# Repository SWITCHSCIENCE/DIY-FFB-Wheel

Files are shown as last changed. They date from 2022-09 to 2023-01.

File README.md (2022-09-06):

# DIY-FFB-Wheel

自作フォースフィードバックステアリングホイール

## 必要なもの

- 「[Arduino Leonard(入出力 5V)](https://www.switch-science.com/catalog/968/)」または「[Pro micro(入出力 5V)](https://www.switch-science.com/catalog/3914/)」などの「Atmega32UX」系列の Arduino 対応ボード
- [Waveshare の CAN for RaspberryPi Pico ボード(入出力 3.3V)](https://www.waveshare.com/pico-can-a.htm)
- [レベル変換ボード(3.3V 系と 5V 系をつなぐ)](https://www.switch-science.com/catalog/1523/)
- [DDT インホイールモーター](https://www.switch-science.com/catalog/8248/)
- [24V20A 安定化電源ユニット](https://www.amazon.co.jp/gp/product/B09PRD74V4)

## ファームウェアビルド

### 必要なライブラリ

- QuickPID(MIT-Licence)
- ArduinoJoystickWithFFB(LGPL-ICENCE)

上記２つのライブラリをライブラリマネージャから探してあらかじめインストールしておいてください。
ArduinoJoystickWithFFB は検索でも見つからないので、以下の操作でインストールしてください。

```コマンドプロンプト
winget install Git # <-まだgitコマンドが使えない場合のみ実行してください
cd C:\Users\<ユーザー名>\Documents\Arduino\libraries
git clone https://github.com/YukMingLaw/ArduinoJoystickWithFFBLibrary
```

## ボードサポートのインストール

Arduino-IDE または Arduino-IDE-V2 または arduino-cli のいずれも利用可能です。
core サポートのインストールが必要です。「Arduino AVR Boards Support」を検索してインストールが必要です。

arduino-cli の場合は以下の操作でコアサポートインストールを行います。

コアサポートインストール

```コマンドプロンプト
arduino-cli core install arduuino:avr
```

## ビルドとフラッシュ

arduino-cli の場合

PC と Arduino-Leonard を USB マイクロケーブルで接続しておいて以下のコマンドでビルドと書き込み。

```コマンドプロンプト
cd firmware
make build flash
```

## 配線

| 名称 | Arduino Leonard | レベル変換 H 側 | レベル変換 L 側 | CAN アダプタ |
| --- | --- | --- | --- | --- |
| RX | 0 番 | HV1 | LV1 | GP1/RX |
| TX | 1 番 | HV2 | LV2 | GP0/TX |
| Config | 2 番 | HV3 | LV3 | GP2 |
| Reset  | 3 番 | HV4 | LV4 | GP3 |
| 5V | 5V | HV | - | VSYS |
| 3.3V | 3.3V | - | LV | - |
| GND | GND | GND | GND | GND |

| 名称 | 電源ユニット | モーター | CAN アダプタ |
| --- | --- | --- | --- |
| プラス | プラス | 赤 | - |
| マイナス | マイナス | 黒 | - |
| CAN-H | - | 黄色 | H |
| CAN-L | - | 白色 | L |
| コンセント H | AC-H | - | - |
| コンセント C | AC-C | - | - |
| コンセント E | AC-E | - | - |

## 3D モデル

- ステアリングバックプレート: steering.stl
- 固定台： holder.stl

双方を[JLCPCB](https://www.pcbway.jp/)にてプリントしてもらう場合は以下のような見積もりになりました。

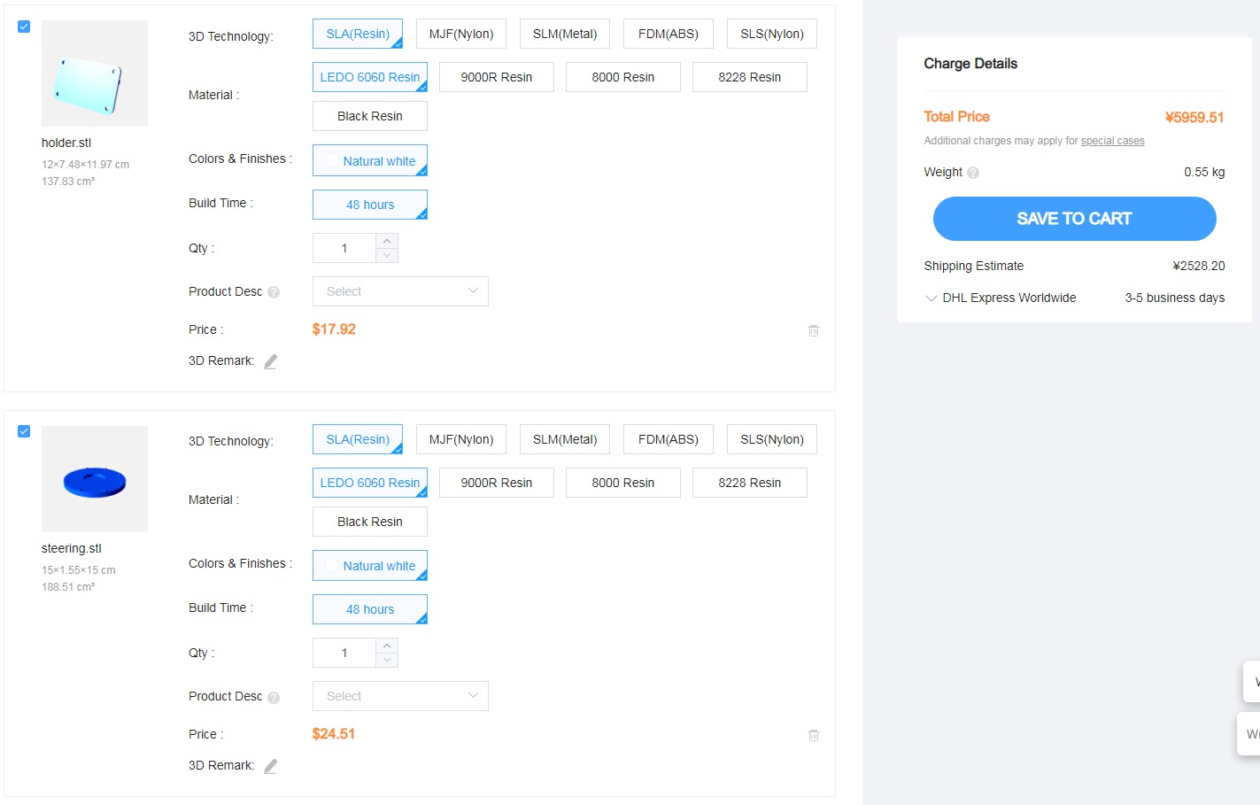
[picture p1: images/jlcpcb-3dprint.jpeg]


SLA 方式にてオーダーした場合、8600 円弱（送料込み） という試算でした。

### その他必要な部品

- M5x20mm ボルト＆ナットセット６本
- M6x20mm ボルト６本

モーターとステアリングバックプレートの固定にはタイヤを外した時のねじをそのまま使います。

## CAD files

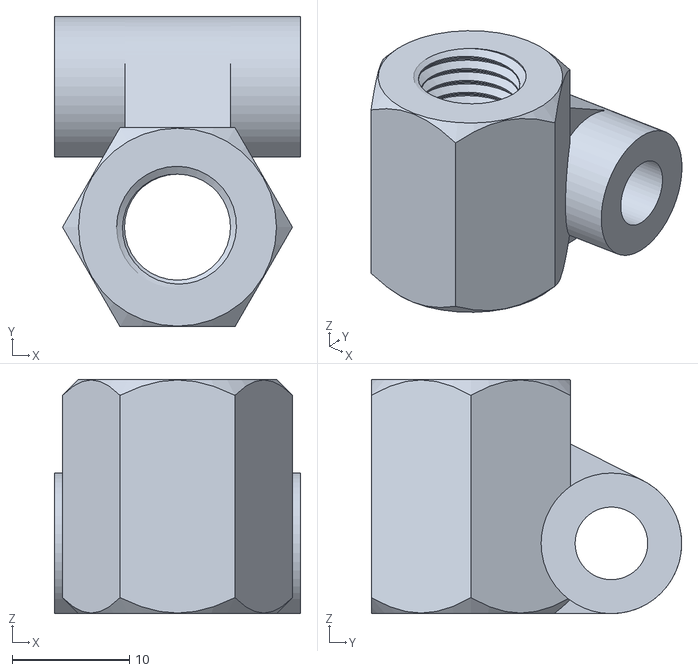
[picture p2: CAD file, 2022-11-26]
models/pedals/for-air-cylinder/air-rod-holder.stl
21.0 x 26.5 x 20.0

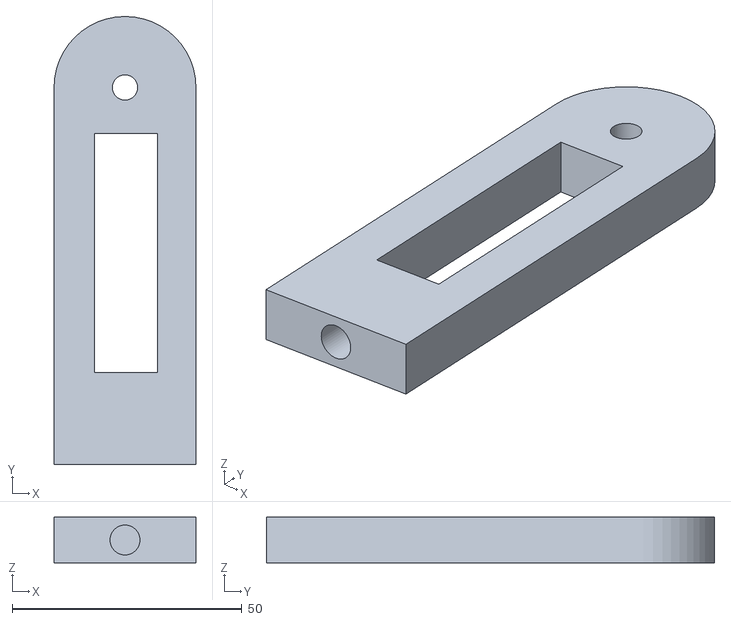
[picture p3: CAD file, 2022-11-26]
models/pedals/for-clutch/rod-angle2.stl
30.9 x 97.4 x 10.0

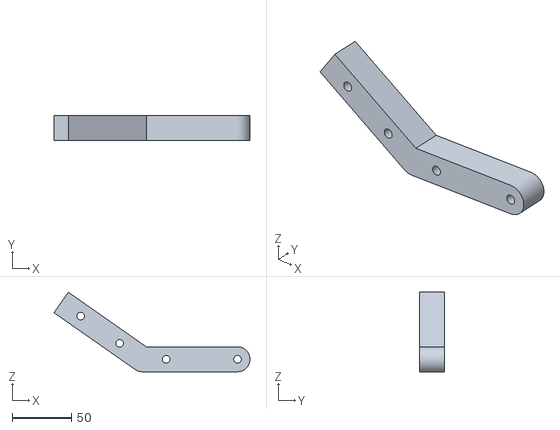
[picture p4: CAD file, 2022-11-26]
models/pedals/for-handbrake/sb-grip-rod.stl
164.8 x 21.0 x 66.9

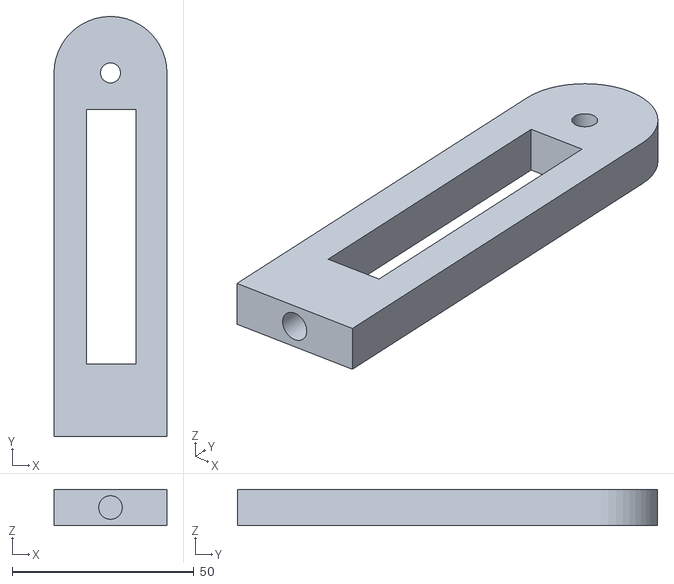
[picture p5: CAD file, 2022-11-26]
models/pedals/for-throttle/rod-angle.stl
31.1 x 115.5 x 10.0

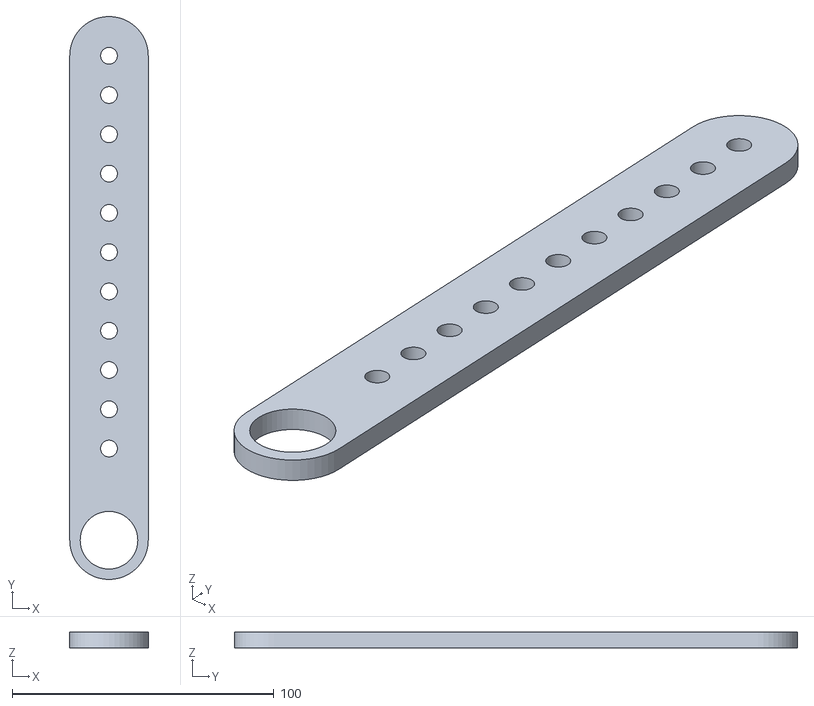
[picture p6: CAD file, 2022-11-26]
models/pedals/pedal-arm.stl
30.0 x 215.0 x 6.00

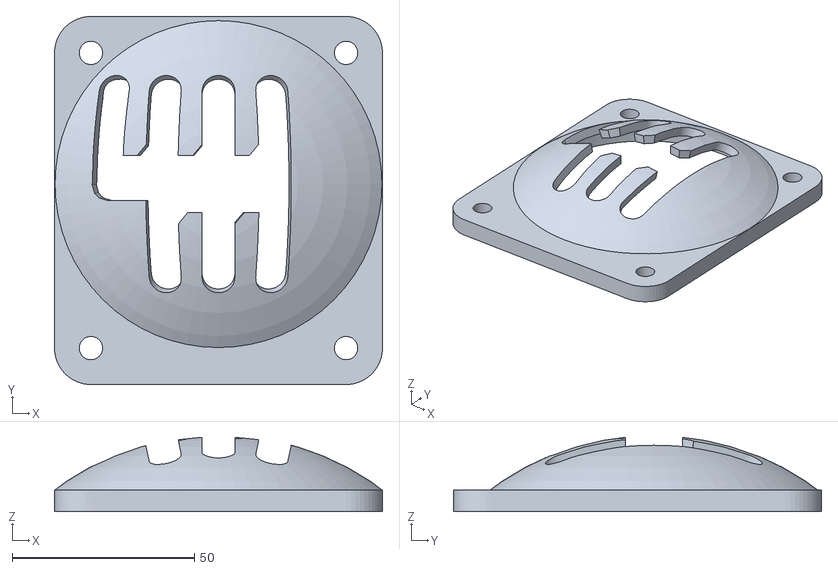
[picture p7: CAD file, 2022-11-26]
models/shifter/h-shifter-top.stl
90.0 x 101.0 x 20.4

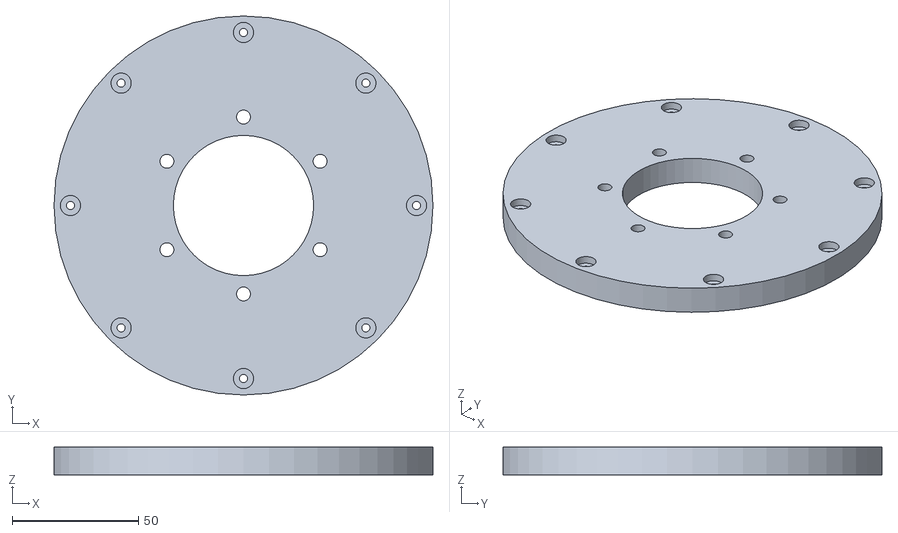
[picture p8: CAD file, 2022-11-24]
models/steering/steering.stl
150.0 x 150.0 x 11.0

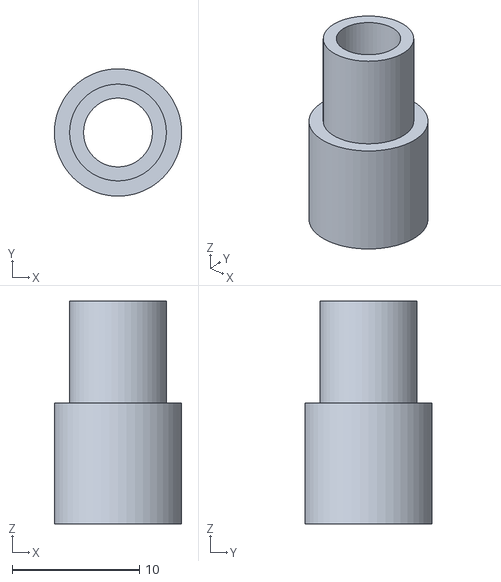
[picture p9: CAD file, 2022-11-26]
models/pedals/for-air-cylinder/air-holder.stl
10.0 x 10.0 x 17.5

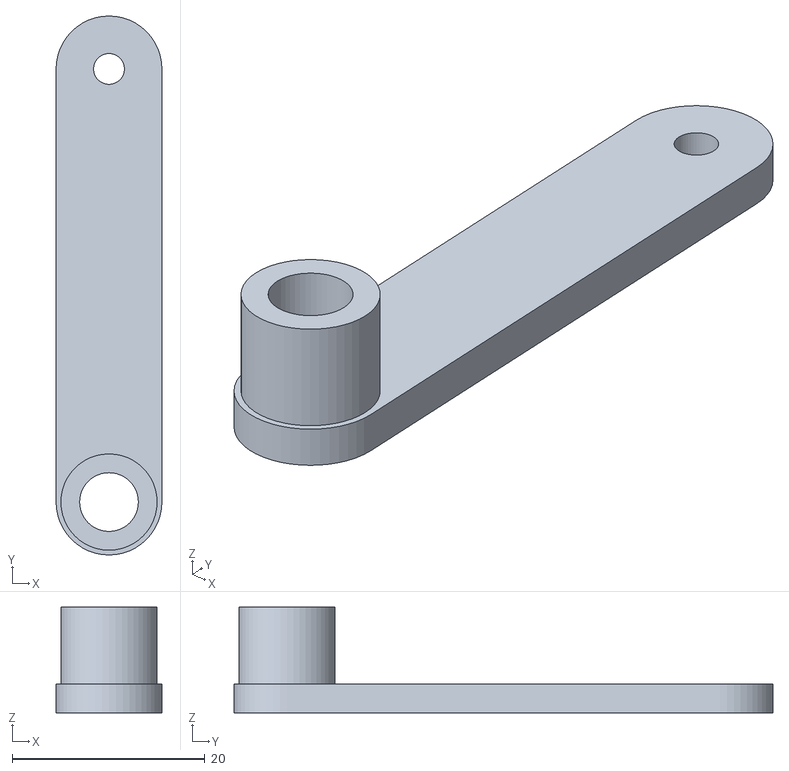
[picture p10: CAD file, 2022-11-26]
models/pedals/for-clutch/potent-rod3.stl
11.0 x 56.0 x 11.0

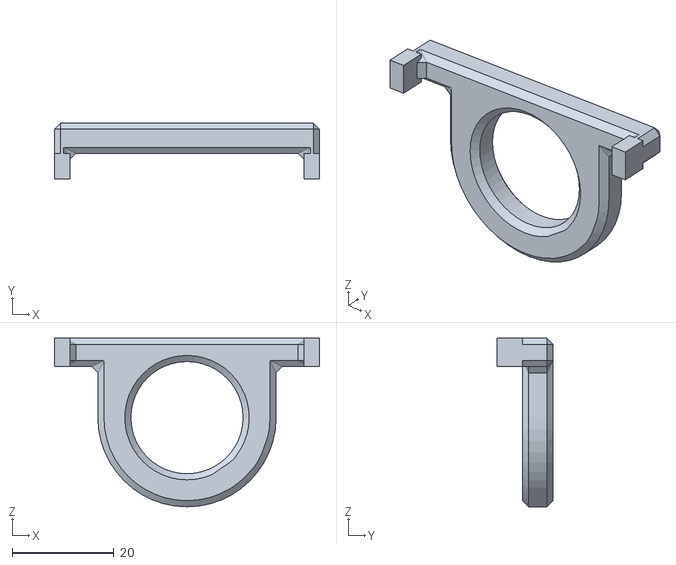
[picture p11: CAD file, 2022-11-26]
models/pedals/for-handbrake/hb-spring-hook.stl
52.0 x 11.0 x 33.1

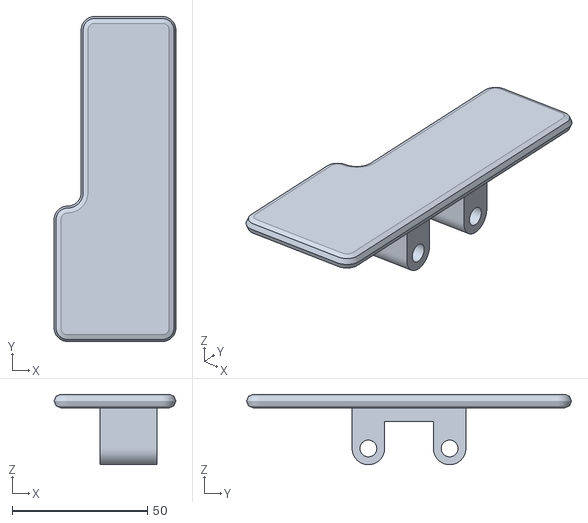
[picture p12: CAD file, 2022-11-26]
models/pedals/for-throttle/pedal2.stl
45.0 x 120.0 x 26.0

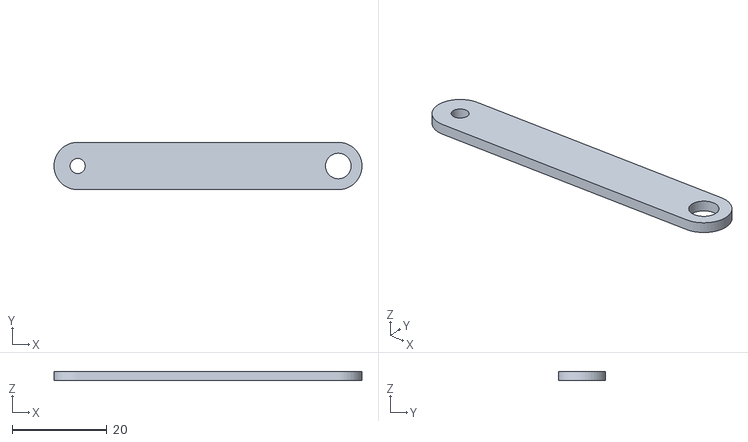
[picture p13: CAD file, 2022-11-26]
models/pedals/potent-rod2.stl
65.0 x 10.0 x 2.00

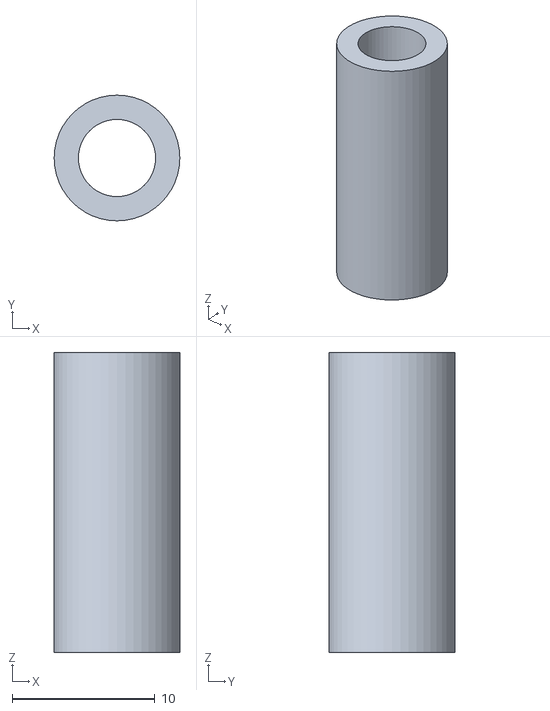
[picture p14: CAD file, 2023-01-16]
models/pedals/spacer/m5-spacer.stl
8.80 x 8.80 x 21.0

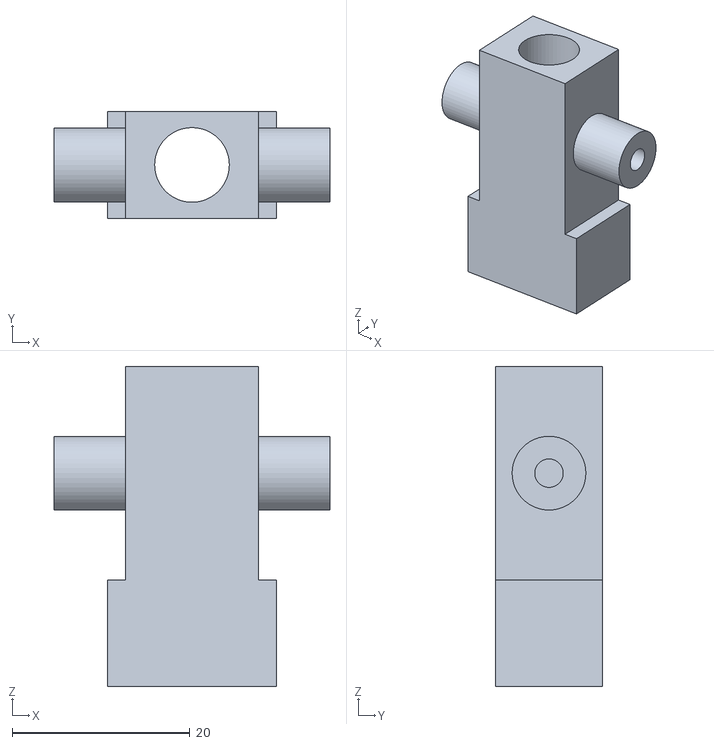
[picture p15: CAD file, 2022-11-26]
models/shifter/h-shifter-2.stl
31.0 x 12.0 x 36.0

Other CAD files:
models/steering/steering-holder.stl
models/pedals/for-clutch/rod-holder2.stl
models/pedals/for-handbrake/sb-grip.stl
models/pedals/for-throttle/potent-rod1.stl
models/pedals/for-air-cylinder/air-holder.blend
models/pedals/for-air-cylinder/air-rod-holder.blend
models/pedals/for-clutch/potent-rod3.blend
models/pedals/for-clutch/rod-angle2.blend
models/pedals/for-clutch/rod-holder2.blend
models/pedals/for-handbrake/hb-spring-hook.blend
models/pedals/for-handbrake/sb-grip-rod.blend
models/pedals/for-handbrake/sb-grip.blend
models/pedals/for-throttle/pedal2.blend
models/pedals/for-throttle/potent-rod1.blend
models/pedals/for-throttle/rod-angle.blend
models/pedals/for-throttle/rod-holder.blend
models/pedals/for-throttle/rod-holder.stl
models/pedals/pedal-arm.blend
models/pedals/pedal-base.blend
models/pedals/pedal-base.stl
models/pedals/pedal1.blend
models/pedals/pedal1.stl
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

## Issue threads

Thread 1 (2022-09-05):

Assetto Corsa Competizione で動かない

nobonobo, 2022-09-05:
CPUビジーになってゲームプロセスの応答がなくなる。要調査。

nobonobo, 2022-09-06:
Assetto Corsa Competizione で動かない
CPUビジーになってゲームプロセスの応答がなくなる。要調査。
Steam版ACCにて発生。

nobonobo, 2022-09-06:
DiRT Rally、DiRT Rally 2.0の双方で良好に動作することを確認。
- DEBUGフラグを有効にした場合はフレームレートが低下する現象あり
- ゲーム内のコントローラー設定のFFB関連パラメータは変更しても反映されない -> #2

nobonobo, 2022-09-06:
Assetto Corsaにて動作することを確認。ただし、まれにACCと同様の状態が発生するようだ。

nobonobo, 2022-09-06:
[Speed Dreams](https://sourceforge.net/projects/speed-dreams/)
オープンソースのレーシングシミュレーター。
FFBとして認識しかけてあきらめるようだ。（何らかの機能の実装不足がありそう）

nobonobo, 2022-09-06:
WRC8 / WRC 9 / WRC10 いずれも良好に動作することを確認。
- ゲーム内のコントローラー設定のFFB関連パラメータは変更しても反映されない -> #2

nobonobo, 2022-09-06:
Euro Track Simulator 2 良好に動作することを確認。
- ゲーム内のコントローラー設定のFFB関連パラメータは変更しても反映されない -> #2

nobonobo, 2022-09-12:
Assetto Corsa Competizione にて、タイトル側の振動数設定を100Hzに下げたら動作することを確認。おそらく、HIDレポートの下り頻度が大きくなりすぎると、デバイス側が処理しきれなくなることで起こる不具合という予想。

nobonobo, 2022-10-16:
rFactor2デモ版とRaceRoomデモ版で試すも動作せず。一部はデモ版はFFB機能に問題があるというコメントあり。

nobonobo, 2022-10-16:
FFBのインターフェースには以下の２種あるみたい。
- 低レベルパワー指定制御
- パターン型パラメータ制御

後者がArduinoJoystickWithFeedbackでは未実装。
これが一部のタイトルでFFBがオフになる原因かもしれない。

nobonobo, 2022-11-18:
V-Rally 4 で試すも問題なく動作することを確認。

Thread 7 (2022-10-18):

3Dプリント支柱は耐熱温度を70度くらい確保したほうが良い

nobonobo, 2022-10-18:
DDTモーターは連続運用中に50~70度（低温やけどの可能性あり）になり、
（ケーブル側のブラケットの側のほうが高熱）
モーターブラケットに接触する支柱はPLAの場合60度程度で軟化してしまう。
固定ねじがやたら緩むなぁと思ったら締めているところのPLAがどんどん肉痩せを起こしていた。

ABS素材(耐熱80度くらい)に変更してからは問題なく使えている。

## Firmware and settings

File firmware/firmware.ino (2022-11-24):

#include "Joystick.h"

#define DEBUG 0
#define ENABLE_FFB 1
#define EXISTS_OPTIONS 1

const float OFFSET = -6;  // Offset for Neutral
const int LOCK2LOCK = 1080;
const int LOCK2LOCK_HALF = LOCK2LOCK / 2;
const int TOTAL_GAIN = 100;                      // max 100%
const float FFBMaxForce = 30000;                 // 15A
const float ElectroMagneticForceCanceler = 150;  // 0.15A
const float DumperFactor = 100;                  // 100rpm -> -10000

// const unsigned long OutputCycle = 16666;  // 16.666ms
const unsigned long OutputCycle = 20000;  // 20ms
const int16_t xMax = 16384;

Joystick_ Joystick(JOYSTICK_DEFAULT_REPORT_ID, JOYSTICK_TYPE_MULTI_AXIS, 16, 1,
                   true, false, true,    // X,Y,Z
                   false, false, false,  // Rx,Ry,Rz
                   false, true,          // Rudder, Throttle,
                   true, true, true);    // Accelerator, Brake, Steering;

Gains mygains[2];
EffectParams myeffectparams[2];
int32_t forces[2] = {0};

typedef struct {
  float Velocity;
  float Current;
  float Angle;
} Record;

bool sequentialMode = true;

int16_t debugV1 = 0;
int16_t debugV1min = 0;
int16_t debugV1max = 0;

void updateValues(int16_t *values) {
  const int pins[] = {A0, A1, A2, A3, A4, A5};
  const int16_t toMax[] = {4, 2, 32767, 32767, 32767, 32767};
  const int16_t toMin[] = {0, -1, 0, 0, 0, 0};
  static int16_t maxValues[] = {-32767, -32767, -32767, -32767, -32767, -32767};
  static int16_t minValues[] = {32767, 32767, 32767, 32767, 32767, 32767};
  static int16_t margins[] = {0, 0, 10, 5, 10, 5};
  for (int i = 0; i < 6; i++) {
    int16_t v = analogRead(pins[i]);
    if (v > maxValues[i]) maxValues[i] = v;
    if (v < minValues[i]) minValues[i] = v;
    int16_t diff = maxValues[i] - minValues[i];
    if (diff < 50) {
      values[i] = 0;
    } else {
      if (i == 0) {
        sequentialMode = false;
        Joystick.setButton(6, false);
        Joystick.setButton(7, false);
      }
      int16_t margin = diff * margins[i] / 100;
      if (v > maxValues[i] - margin) v = maxValues[i] - margin;
      values[i] = map(v, minValues[i] + margin, maxValues[i] - margin, toMin[i],
                      toMax[i]);
    }
  }
}

int16_t be2_to_int16(const uint8_t *data) {
  return ((uint16_t)data[0] << 8) | ((uint16_t)data[1] << 0);
}

Record decode(uint8_t *b) {
  Record rec;
  rec.Velocity = (float)be2_to_int16(&b[0]);
  rec.Current = (float)be2_to_int16(&b[2]);
  rec.Angle = ((float)((uint16_t)(b[4] & 0x7f) << 8 | ((uint16_t)b[5] << 0))) *
              360 / 32768;
  return rec;
}

void sendCmd(int32_t id, uint8_t *data, size_t len) {
  static uint8_t buff[13];
  buff[0] = len;
  buff[1] = (id >> 24) & 0xff;
  buff[2] = (id >> 16) & 0xff;
  buff[3] = (id >> 8) & 0xff;
  buff[4] = (id >> 0) & 0xff;
  memset(&buff[5], 0, 8);
  memcpy(&buff[5], data, len);
  Serial1.write(buff, sizeof(buff));
}

void sendValue(int16_t v) {
  uint16_t v16 = (uint16_t)v;
  static uint8_t buff[13];
  buff[0] = 2;
  buff[1] = 0;
  buff[2] = 0;
  buff[3] = 0;
  buff[4] = 0x32;
  buff[5] = v16 >> 8 & 0xff;
  buff[6] = v16 >> 0 & 0xff;
  buff[7] = 0;
  buff[8] = 0;
  buff[9] = 0;
  buff[10] = 0;
  buff[11] = 0;
  buff[12] = 0;
  Serial1.write(buff, sizeof(buff));
}

void printFrame(uint32_t id, uint8_t *buff, size_t len) {
  static char b[7];
  sprintf(b, "%03X", id);
  Serial.print("id:");
  Serial.print(b);
  Serial.print(" raw:");
  for (int i = 0; i < len; i++) {
    sprintf(b, "%02X", buff[i]);
    Serial.print(b);
  }
  Serial.println();
}

void SetupDDT() {
  const int config = 2;
  const int reset = 3;
  Serial1.begin(500000);
  Serial1.setTimeout(100);
  pinMode(config, OUTPUT);
  pinMode(reset, OUTPUT);
  digitalWrite(config, 0);
  digitalWrite(reset, 1);
  delay(100);
  digitalWrite(reset, 0);
  delay(100);
  digitalWrite(config, 1);
  delay(100);
  Serial1.print("AT+MODE=PROTOL\r");
  Serial.print(Serial1.readString());
  delay(100);
  Serial1.print("AT+CAN=500,0,NDTF\r");
  Serial.print(Serial1.readString());
  delay(100);
  Serial1.print("AT+CANFLT=0,0,OFF\r");
  Serial.print(Serial1.readString());
  delay(100);
  Serial1.print("AT+UART=500000,8,1,NONE,NFC\r");
  Serial.print(Serial1.readString());
  delay(100);
  digitalWrite(config, 0);
  digitalWrite(reset, 1);
  delay(100);
  digitalWrite(reset, 0);
  delay(100);
  uint32_t id;
  uint8_t buff[16];
  size_t len;
  Serial.println("0x109");
  uint8_t b109[] = {1};
  sendCmd(0x109, b109, sizeof(b109));
  id = readFrame(buff, &len);
  printFrame(id, buff, len);
  /*
  Serial.print("0x107: ");
  uint8_t b107[] = {0x01, 0x01, 0x03, 0x04, 0xaa};
  sendCmd(0x107, b107, sizeof(b107));
  id = readFrame(buff, &len);
  printFrame(id, buff, len);
  */
  Serial.print("0x106: ");
  uint8_t b106[] = {0x80};
  sendCmd(0x106, b106, sizeof(b106));
  id = readFrame(buff, &len);
  printFrame(id, buff, len);
  Serial.print("0x105: ");
  // Control Mode
  // 0:Voltage-Open
  // 1:Current Loop
  // 2:Velocity Loop
  // 3:Angle Loop
  uint8_t b105[] = {0x00};
  sendCmd(0x105, b105, sizeof(b105));
  id = readFrame(buff, &len);
  printFrame(id, buff, len);
}

int getShift(int16_t x, int16_t y) {
  switch (x) {
    case 0:
      switch (y) {
        default:
          return 1;
        case 0:
          return 0;
        case -1:
          return 2;
      }
    case 1:
      switch (y) {
        default:
          return 3;
        case 0:
          return 0;
        case -1:
          return 4;
      }
    case 2:
      switch (y) {
        default:
          return 5;
        case 0:
          return 0;
        case -1:
          return 6;
      }
    default:
      switch (y) {
        default:
          return 7;
        case 0:
          return 0;
        case -1:
          return -1;
      }
  }
}

#define N 13

uint32_t readFrame(uint8_t *data, size_t *len) {
  *len = 0;
  static uint8_t buff[N];
  static uint8_t index = 0;
  while (Serial1.available()) {
    uint8_t b = Serial1.read();
    // Serial.println(b, HEX);
    buff[index++] = b;
    index %= N;
    if (b == 0 && buff[(index + N - 2) % N] == 0x55) {
      uint8_t ri = (index + N - 13) % N;
      if (buff[ri] != 8) continue;
      uint32_t id = 0;
      for (int i = 0; i < 4; i++) {
        id <<= 8;
        id |= (uint32_t)(buff[(ri + i + 1) % N]);
      }
      for (int i = 0; i < 8; i++) {
        *(data++) = buff[(ri + i + 5) % N];
        (*len)++;
      }
      return id;
    }
  }
  return 0;
}

void request(bool force = false) {
  static unsigned long requested = 0;
  static uint8_t b[] = {0x01, 0x01, 0x02, 0x04, 0x55};
  unsigned long now = micros();
  if (force || now - requested > OutputCycle) {
    sendCmd(0x107, b, sizeof(b));
    requested = now;
  }
}

void setup() {
#if DEBUG > 0
  Serial.begin(230400);
  while (!Serial) delay(100);
#endif
#if ENABLE_PID > 0
  Input = 0;
  Setpoint = 0;
  myPID.SetOutputLimits(-LockMaxForce, LockMaxForce);
  // myPID.SetSampleTimeUs(10000);
  myPID.SetMode(myPID.Control::automatic);
  myPID.SetTunings(Kp, Ki, Kd);
  // myPID.SetDerivativeMode(QuickPID::dMode::dOnError);
#endif
  SetupDDT();
  Serial.println("start!");
  pinMode(A0, INPUT);
  pinMode(A1, INPUT);
  pinMode(A2, INPUT);
  pinMode(A3, INPUT);
  pinMode(A4, INPUT);
  pinMode(A5, INPUT);
  // pinMode(A6, INPUT);
  pinMode(9, OUTPUT);
  pinMode(6, OUTPUT);
  pinMode(7, OUTPUT);
  Joystick.setXAxisRange(-xMax, xMax);
  Joystick.setYAxisRange(-32767, 32767);
  Joystick.setZAxisRange(0, 32767);
  Joystick.setRxAxisRange(-32767, 32767);
  Joystick.setRyAxisRange(-32767, 32767);
  Joystick.setRzAxisRange(-32767, 32767);
  Joystick.setRudderRange(0, 32767);
  Joystick.setThrottleRange(0, 32767);
  Joystick.setAcceleratorRange(0, 32767);
  Joystick.setBrakeRange(0, 32767);
  Joystick.setSteeringRange(-xMax, xMax);

  // set X Axis gains
  mygains[0].totalGain = TOTAL_GAIN;  // 0-100
  mygains[0].springGain = 100;        // 0-100
  mygains[0].constantGain = 100;      // 0-100
  mygains[0].rampGain = 100;          // 0-100
  mygains[0].squareGain = 100;        // 0-100
  mygains[0].sineGain = 100;          // 0-100
  mygains[0].triangleGain = 100;      // 0-100
  mygains[0].sawtoothdownGain = 100;  // 0-100
  mygains[0].sawtoothupGain = 100;    // 0-100
  mygains[0].springGain = 100;        // 0-100
  mygains[0].damperGain = 100;        // 0-100
  mygains[0].frictionGain = 100;      // 0-100
  mygains[0].customGain = 100;        // 0-100
  // enable gains REQUIRED
  Joystick.setGains(mygains);
  Joystick.begin(false);
}

void loop() {
  static double angle = 0;
  static float offsetAngle = 0;
  static float oldAngle = 0;
  static uint8_t buff[8];
  static int shift = 0;
  static size_t len;
  static int cnt = 0;

  int16_t x =
      map(-angle * 8, -LOCK2LOCK_HALF * 8, LOCK2LOCK_HALF * 8, -xMax, xMax);
  uint32_t tm = micros();
  static uint32_t last = 0;
  if (tm - last > 500) {
    // Steering wheel
    Joystick.setXAxis(x);
    Joystick.setSteering(x);
    // Send HID data to PC
    Joystick.sendState();

    // caculate forces
    myeffectparams[0].springMaxPosition = xMax;
    myeffectparams[0].springPosition = x;
    Joystick.setEffectParams(myeffectparams);
    Joystick.getForce(forces);
    last = tm;
  }

  cnt++;

  request();
  uint32_t id = readFrame(buff, &len);
  if (id == 151) {
    // Serial.println(micros());
    Record rec = decode(buff);
    if (oldAngle < 90 && rec.Angle > 270) {
      offsetAngle -= 360;
    }
    if (oldAngle > 270 && rec.Angle < 90) {
      offsetAngle += 360;
    }
    oldAngle = rec.Angle;
    angle = offsetAngle + rec.Angle + OFFSET;

#if EXISTS_OPTIONS > 0
    static int16_t values[6];

    updateValues(values);

    if (sequentialMode) {
      switch (values[1]) {
        default:
          Joystick.setButton(6, true);
          Joystick.setButton(7, false);
          break;
        case 0:
          Joystick.setButton(6, false);
          Joystick.setButton(7, false);
          break;
        case -1:
          Joystick.setButton(6, false);
          Joystick.setButton(7, true);
          break;
      }
    } else {
      shift = getShift(values[0], values[1]);
      for (int i = 0; i < 7; i++) {
        Joystick.setButton(i + 8, i + 1 == shift);
      }
      Joystick.setButton(7 + 8, shift == -1);
    }
    Joystick.setHatSwitch(0, -1);

    // Handbrake
    Joystick.setZAxis(values[2]);
    // Joystick.setRudder(values[2]);

    // Throttle
    // Joystick.setZAxis(values[3]);
    Joystick.setThrottle(values[3]);

    // Brake
    // Joystick.setRzAxis(values[4]);
    Joystick.setBrake(values[4]);

    // Clutch
    // Joystick.setRyAxis(values[5]);
    Joystick.setAccelerator(values[5]);
#endif

    // Recv HID-PID data from PC
    float FFBForce = (float)(forces[0]) / 255 * FFBMaxForce;
    float output = FFBForce;
    output += ElectroMagneticForceCanceler * rec.Velocity;
    output -= rec.Velocity * DumperFactor;
    if (output > 32767) output = 32767;
    if (output < -32767) output = -32767;
#if DEBUG > 0
    Serial.print(millis());
    Serial.print(": a:");
    Serial.print(rec.Angle);
    Serial.print(": c:");
    Serial.print(rec.Current);
    Serial.print(": v:");
    Serial.print(rec.Velocity);
    Serial.print(": X:");
    Serial.print(values[0]);
    Serial.print(": Y:");
    Serial.print(values[1]);
    Serial.print(": Shift:");
    Serial.print(shift);
    Serial.print(": A:");
    Serial.print(angle);
    Serial.print(" FFB:");
    Serial.print(FFBForce);
    Serial.print(" Output:");
    Serial.print(output);
    Serial.print(" Count:");
    Serial.print(cnt);
    Serial.println();
#endif
    cnt = 0;
    sendValue((int16_t)(output));
  }
}

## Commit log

2022-09-06 fix stl scale
    [holder.stl, steering.stl]
2022-09-06 3d-print cost fix
2022-11-24 fix steering-holder model
    [holder.blend, holder.stl, steering-holder.blend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]
2022-11-24 fix steering stl
    [steering.stl]
2022-11-26 add other models
    [air-holder.blend, air-holder.stl, air-rod-holder.blend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]
2022-11-26 add pedal-arm.stl
    [pedal-arm.blend, pedal-arm.stl]
2023-01-16 add spacer
    [m5-spacer.blend, m5-spacer.stl, m5x13-spacer.blend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]
